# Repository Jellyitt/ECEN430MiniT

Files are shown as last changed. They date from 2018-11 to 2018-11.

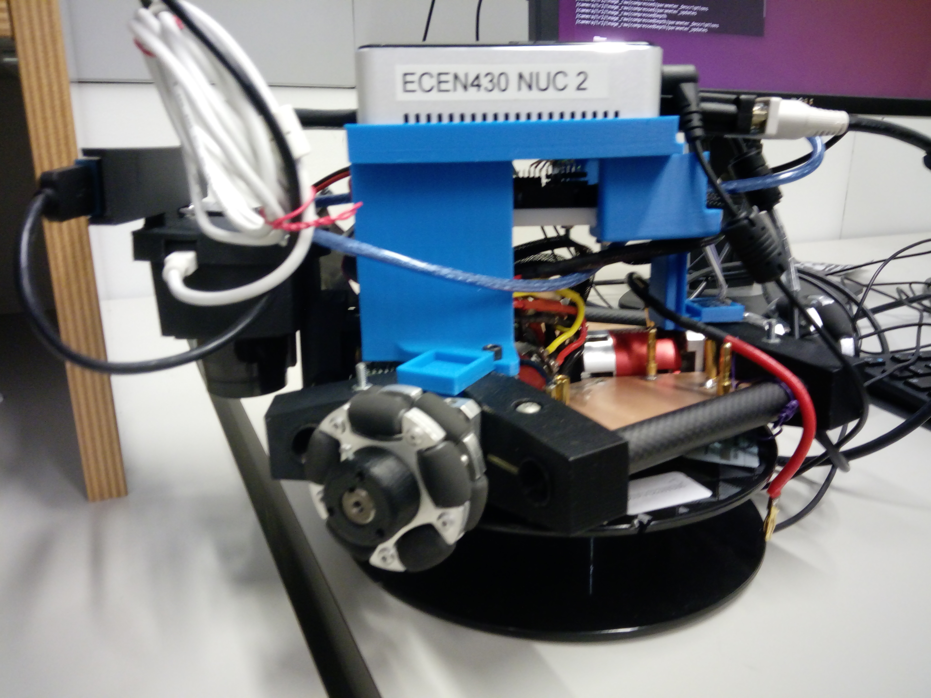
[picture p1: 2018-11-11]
Development Files/Hardware/IMG_20181106_105924.jpg

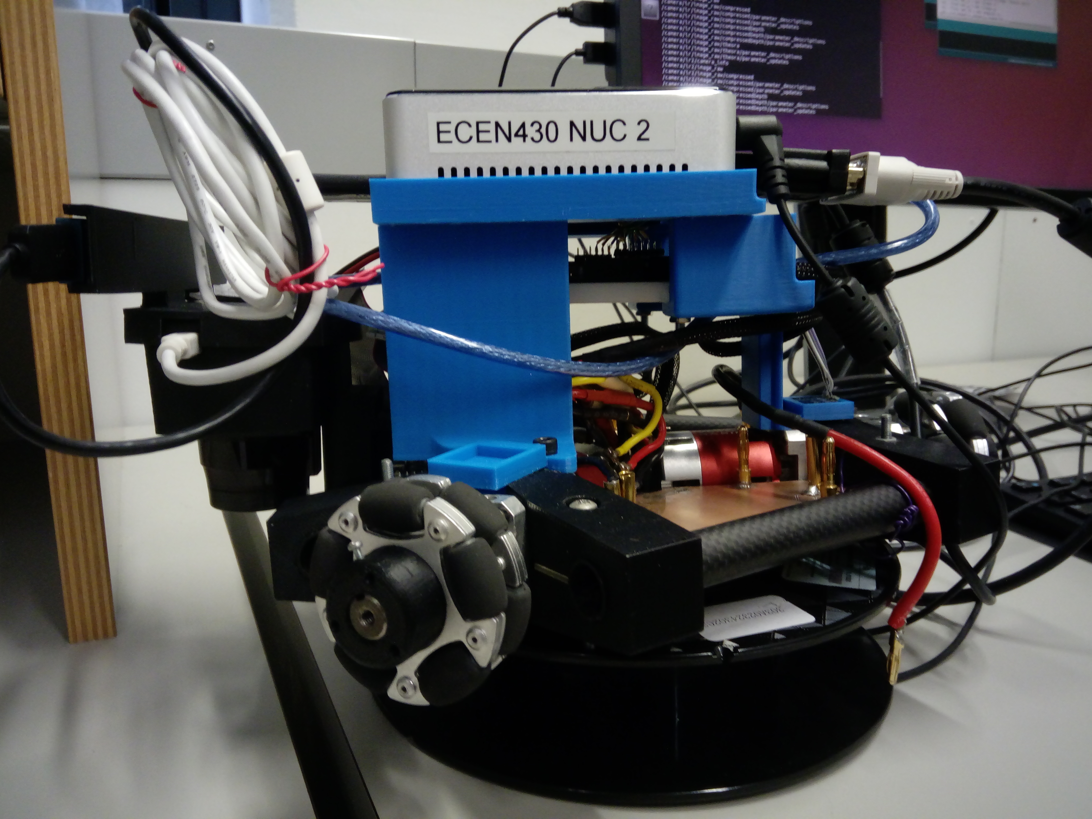
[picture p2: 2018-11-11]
Development Files/Hardware/IMG_20181106_105932.jpg

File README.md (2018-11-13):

# ECEN 430 Autonomous Vehicle Files

This was a collaborative project worked on during the course of ECEN 430 (2018)- Advanced Mechatronic Engineering 2: Intelligence and Design.

This autonomous vehicle imployed a ROS based system across a Intel NUC and a Laptop. Both computer systems were operating on Ubuntu 16.04.4. This was implemented on the Mini Triangle robot platform

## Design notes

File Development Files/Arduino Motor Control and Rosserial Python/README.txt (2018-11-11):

This system runs arduino 1.8.5
The code is a ROS node that communicates with the NUC through the rosserial_python node
This node subscribes to /cmd_vel and sends this for motor and speed control. While it publishes IMU data as geometry_msgs/Twist data type

How to run the arduino from terminal:
cd arduino-1.8.5/
./arduino

Note: Pressing tab on the keyboard autocompletes the word

File name:
Arduino Code - Motor Control - Bosch IMU -> Code using Bosch IMU
Arduino Code - Motor Control - MPU6050 IMU -> Code using MPU6050 IMU, used in the current system

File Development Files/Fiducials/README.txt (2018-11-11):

How to run fiducials in the current system set-up.
On the NUC currently:

Without launch files:
roscore
NT: roslaunch realsense_camera r200_nodelet_default.launch
NT: rosrun aruco_detect aruco_detect camera:=/camera/color/image_raw camera_info:=/camera/color/camera_info
NT: roslaunch fiducial_slam fiducial_slam.launch
NT: roslaunch fiducial_slam fiducial_rviz.launch

With launch files:
roscore
NT: cd catkin_ws/src/launch_file/launch
roslaunch min_launch2.launch

Note: NT = New Terminal

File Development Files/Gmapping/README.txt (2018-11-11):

How to run gmapping in the current system set-up.

Ensure both laptop and NUC are connected to the modesttriangle network.

Firstly turn on the NUC:
roscore
NT: cd catkin_ws/src/launch_file/launch
roslaunch min_launch.launch

On the laptop:
ssh modesttrianglenuc@modesttrianglenuc-desktop
NT: cd catkin_ws/src/slam_gmapping/gmapping/launch
roslaunch <File name>
NT: rviz

Note: NT = open new terminal window
Note: min_launch.launch = launches rosserial python node (arduino), Lidar, Camera and static transforms

<File name>:
gmap_move.launch -> runs gmapping, map server CO249, move base
gmap2.launch -> runs gmapping, map server CO level two floor plan
gmap249.launch -> runs gmapping, map server CO249
gmapping.launch -> runs gmapping node

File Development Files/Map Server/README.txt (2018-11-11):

How to run map_server in the current system set-up.

Ensure both laptop and NUC are connected to the modesttriangle network.

Firstly turn on the NUC:
roscore
{ NT: cd catkin_ws/src/launch_file/launch
roslaunch min_launch.launch }

On the laptop:
ssh modesttrianglenuc@modesttrianglenuc-desktop
NT: cd catkin_ws/src/launch_file/launch
roslaunch map_server.launch
NT: rviz

Note: NT = open new terminal window
      {} = optional

File name:
min_launch.launch = launches rosserial python node (arduino), Lidar, Camera and static transforms

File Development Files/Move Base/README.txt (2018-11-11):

How to run move_base in the current system set-up.

Ensure both laptop and NUC are connected to the modesttriangle network.

Firstly turn on the NUC:
roscore
NT: cd catkin_ws/src/launch_file/launch
roslaunch min_launch.launch

On the laptop:
ssh modesttrianglenuc@modesttrianglenuc-desktop
NT: cd catkin_ws/src/launch_file/launch
roslaunch <File name>
NT: rviz

Note: NT = open new terminal window
Note: min_launch.launch = launches rosserial python node (arduino), Lidar, Camera and static transforms

<File name>:
move_base.launch -> runs only move base node
move_base2.launch -> runs move base, map server, static transform
amcl_omni.launch -> runs move base, map server, static transform, amcl
all.launch -> runs move base, map server, static transform, amcl (old values in amcl)

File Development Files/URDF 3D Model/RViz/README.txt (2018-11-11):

How to run URDF model for RViz in the current system set-up.

Ensure both laptop and NUC are connected to the modesttriangle network.

Firstly turn on the NUC:
roscore
NT: cd catkin_ws/src/launch_file/launch
roslaunch min_launch.launch

On the laptop:
ssh modesttrianglenuc@modesttrianglenuc-desktop
NT: cd catkin_ws/src/simpleModel
rosrun simpleModel urdf_visualize.launch model:='$(find simpleModel)/urdf/simpleModel.urdf'

Note: NT = open new terminal window
Note: min_launch.launch = launches rosserial python node (arduino), Lidar, Camera and static transforms

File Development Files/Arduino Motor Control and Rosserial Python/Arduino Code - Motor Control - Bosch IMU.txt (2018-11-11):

//Bosch BNO055 libraries
#include <Wire.h>
#include <Adafruit_Sensor.h>
#include <Adafruit_BNO055.h>
#include <utility/imumaths.h>

//ROS libraries
#include <ros.h>
#include <ArduinoHardware.h>
#include <geometry_msgs/Twist.h>

//#define led_pin 13
#define max_x 1.5
#define max_y 1.5
#define max_Th 3

#define BNO055_SAMPLERATE_DELAY_MS (1000)

Adafruit_BNO055 bno = Adafruit_BNO055();

volatile float linear_v_x, linear_v_y, linear_v_z;
volatile float angular_v_x, angular_v_y, angular_v_z;

ros::NodeHandle nh;

//motor 1 -- Err(LOW) = forward motion/counter-clockwise
#define PWM1 6 //Port A, pin 31
#define En1 8 //Port A, pin 23
#define Err1 3 //Port A, pin 25

//motor 2 -- Err(HIGH) = forward motion/clockwise
#define PWM2 10 //Port A, pin 29
#define En2 7 //Port A, pin 19
#define Err2 5 //Port A, pin 21

//motor 3 -- Err(HIGH) = clockwise motion
#define PWM3 9 //Port A, pin 27
#define En3 4 //Port A, pin 15
#define Err3 2 //Port A, pin 17

void messageCb(const geometry_msgs::Twist& val){
  float val_x = val.linear.x;
  float val_y = val.linear.y;
  float val_Th = val.angular.z;
  int speed_x, speed_y, speed_Th;
  if(val_x == 0 && val_y == 0 && val_Th == 0){
    digitalWrite(En1, LOW);
    digitalWrite(En2, LOW);
    digitalWrite(En3, LOW);
  }
  else{
    int x = calcX(val_x);
    int y = calcY(val_y);
    int Th = calcTh(val_Th);

    if(x != 0 && Th != 0){
      if(Th > 0){
        speed_x = (-1*x)/4 + Th;
        speed_y = x/1.5 + Th;
        speed_Th = (-1*Th);
        }
        else{
        speed_x = (-1*x)/1.5 + Th;
        speed_y = x/4 + Th;
        speed_Th = (-1*Th);
        }
      }
    else{
      speed_x = (-1*x) + Th;
      speed_y = x + Th;
      speed_Th = (-1*Th);
    }
    
    set_dir(sign(speed_x, Th), sign(speed_y, Th), sign(0, speed_Th * -1));
    drive_motors(min(abs(0.7*speed_x), 229), min(abs(0.7*speed_y), 229), min(0.7*abs(speed_Th), 229));
  }
}

ros::Subscriber<geometry_msgs::Twist> sub("/cmd_vel", &messageCb );
geometry_msgs::Twist imu_msg;
ros::Publisher imu_data("imu/data", &imu_msg);

void setup() {
  TCCR1B = TCCR1B & B11111000 | B00000010; // for PWM frequency of 3921.16 Hz  -> pins 9 + 10
  TCCR2B = TCCR2B & B11111000 | B00000010; // for PWM frequency of 3921.16 Hz  -> pin 11

  pinMode(PWM3, OUTPUT);
  pinMode(En3, OUTPUT);
  pinMode(Err3, OUTPUT);
  pinMode(PWM2, OUTPUT);
  pinMode(En2, OUTPUT);
  pinMode(Err2, OUTPUT);
  pinMode(PWM1, OUTPUT);
  pinMode(En1, OUTPUT);
  pinMode(Err1, OUTPUT);
  //pinMode(led_pin, OUTPUT);
  
  linear_v_x = 0;
  linear_v_y = 0;
  linear_v_z = 0;
  angular_v_x = 0;
  angular_v_y = 0;
  angular_v_z = 0;
  
  bno.setExtCrystalUse(true);
 
  nh.initNode();
  nh.subscribe(sub);
  nh.advertise(imu_data);
}

void loop(){
  while(!nh.connected()){
  nh.spinOnce();
  imu_update();
  }
  
  //digitalWrite(led_pin, LOW);
  //delay(100);
  //digitalWrite(led_pin,LOW);
}

void imu_update(){
  imu::Vector<3> gyro = bno.getVector(Adafruit_BNO055::VECTOR_GYROSCOPE);
  linear_v_x = gyro.x();
  linear_v_y = gyro.y();
  linear_v_z = gyro.z();

  imu::Vector<3> accel = bno.getVector(Adafruit_BNO055::VECTOR_ACCELEROMETER);
  angular_v_x = accel.x();
  angular_v_y = accel.y();
  angular_v_z = accel.z();

  delay(BNO055_SAMPLERATE_DELAY_MS);

  // update geometry msg
  imu_msg.linear.x= linear_v_x;
  imu_msg.linear.y= linear_v_y;
  imu_msg.linear.z= linear_v_z;
  imu_msg.angular.x= angular_v_x;
  imu_msg.angular.y= angular_v_y;
  imu_msg.angular.z= angular_v_z;

  imu_data.publish(&imu_msg);

}

//Motor speeds
int calcX(float i){
  float speedFrac = i/max_x;
  return (int)(speedFrac*250);
}

int calcY(float i){
  float speedFrac = i/max_y;
  return (int)(speedFrac*250);
}

int calcTh(float i){
  float speedFrac = i/max_Th;
  return (int)(speedFrac*250);
}

//Motor Direction
int sign(float spd, float turn){
  if(turn != 0){
    if(turn < 0){
      return LOW;
    }
    else{
      return HIGH;
    }
  }
  else{
  if(spd < 0){
    return LOW;
  }
  else{
    return HIGH;
  }
  }
}

//Set motors
void set_dir(int sgn1, int sgn2, int sgn3){
  digitalWrite(Err1, sgn1);
  digitalWrite(Err2, sgn2);
  digitalWrite(Err3, sgn3);
}

void drive_motors(int pwm_1, int pwm_2, int pwm_3){
  digitalWrite(En1, HIGH);
  digitalWrite(En2, HIGH);
  digitalWrite(En3, HIGH);
  analogWrite(PWM1, pwm_1);
  analogWrite(PWM2, pwm_2);
  analogWrite(PWM3, pwm_3);
}

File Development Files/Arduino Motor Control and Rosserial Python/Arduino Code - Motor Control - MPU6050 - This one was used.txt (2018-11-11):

#include <MPU6050_tockn.h>
#include <elapsedMillis.h>
#include <ros.h>
#include <std_msgs/UInt16.h>
#include <geometry_msgs/Twist.h>

float max_x = 1.5;
float max_y = 1.5;
float max_Th = 5;

volatile float linear_v_x, linear_v_y, linear_v_z;
volatile float angular_v_x, angular_v_y, angular_v_z;

unsigned long publish_interval = 20; //ms

ros::NodeHandle nh;
MPU6050 mpu6050(Wire); //create mpu instance using wire lib

elapsedMillis timeElapsed;
elapsedMillis timePublish;

//motor 1 -- Err(LOW) = forward motion/counter-clockwise
#define PWM1 6 //Port A, pin 31
#define En1 8 //Port A, pin 23
#define Err1 3 //Port A, pin 25

//motor 2 -- Err(HIGH) = forward motion/clockwise
#define PWM2 10 //Port A, pin 29
#define En2 7 //Port A, pin 19
#define Err2 5 //Port A, pin 21

//motor 3 -- Err(HIGH) = clockwise motion
#define PWM3 9 //Port A, pin 27
#define En3 4 //Port A, pin 15
#define Err3 2 //Port A, pin 17

void messageCb(const geometry_msgs::Twist& val){
  float val_x = val.linear.x;
  float val_y = val.linear.y;
  float val_Th = val.angular.z;
//  int speed_x, speed_y, speed_Th;
  if(val_x == 0 && val_y == 0 && val_Th == 0){
    digitalWrite(En1, LOW);
    digitalWrite(En2, LOW);
    digitalWrite(En3, LOW);
  }
  else{
    int x = calcX(val_x);
    int y = calcY(val_y);
    int Th = calcTh(val_Th);
//    if(Th > 0){
//    speed_x = (-1*x)/2 - Th;
//    speed_y = x/2 - Th;
//    }
//    else{
    int speed_x = (-1*x) - Th;
    int speed_y = x - Th;
//}
    int speed_Th = (-1*Th);
    set_dir(sign(speed_x), sign(speed_y), sign(speed_Th));
    drive_motors(min(abs(0.9*speed_x), 229), min(abs(0.9*speed_y), 229), min(0.9*abs(speed_Th), 229));
  }
}

ros::Subscriber<geometry_msgs::Twist> sub("/cmd_vel", &messageCb );
geometry_msgs::Twist imu_msg;
ros::Publisher imu_data("imu_data", &imu_msg);

void setup() {
  TCCR1B = TCCR1B & B11111000 | B00000010; // for PWM frequency of 3921.16 Hz  -> pins 9 + 10
  TCCR2B = TCCR2B & B11111000 | B00000010; // for PWM frequency of 3921.16 Hz  -> pin 11
 
  pinMode(PWM3, OUTPUT);
  pinMode(En3, OUTPUT);
  pinMode(Err3, OUTPUT);
  pinMode(PWM2, OUTPUT);
  pinMode(En2, OUTPUT);
  pinMode(Err2, OUTPUT);
  pinMode(PWM1, OUTPUT);
  pinMode(En1, OUTPUT);
  pinMode(Err1, OUTPUT);

  mpu6050.begin();
  mpu6050.calcGyroOffsets(true);

  nh.initNode();
  nh.subscribe(sub);
  nh.advertise(imu_data);

}

void loop(){
  nh.spinOnce();
 
  if (timePublish >= publish_interval){
    imu_update();
    timePublish= 0;
  }

}

void imu_update(){
  mpu6050.update();

  // Update local variables 
  linear_v_x +=  mpu6050.getAccX()*(timeElapsed/1000.00);
  linear_v_y += mpu6050.getAccY()*(timeElapsed/1000.00);
  linear_v_z = mpu6050.getAccZ()*(timeElapsed/1000.00);
  angular_v_x = getGyroAngleX();
  angular_v_y = getGyroAngleX();
  angular_v_z = getGyroAngleX();
  timeElapsed = 0; //restart timer

  // update geometry msg
  imu_msg.linear.x= linear_v_x;
  imu_msg.linear.y= linear_v_y;
  imu_msg.linear.z= linear_v_z;
  imu_msg.angular.x= angular_v_x;
  imu_msg.angular.y= angular_v_y;
  imu_msg.angular.z= angular_v_z;

  imu_data.publish(&imu_msg);
  
}

int calcX(float i){
  float speedFrac = i/max_x;
  return (int)(speedFrac*250);
}

int calcY(float i){
  float speedFrac = i/max_y;
  return (int)(speedFrac*250);
}

int calcTh(float i){
  float speedFrac = i/max_Th;
  return (int)(speedFrac*250);
}

int sign(float i){
  if(i < 0){
    return LOW;
  }
  else{
    return HIGH;
  }
}

void set_dir(int sgn1, int sgn2, int sgn3){
  digitalWrite(Err1, sgn1);
  digitalWrite(Err2, sgn2);
  digitalWrite(Err3, sgn3);
}

void drive_motors(int pwm_1, int pwm_2, int pwm_3){
  digitalWrite(En1, HIGH);
  digitalWrite(En2, HIGH);
  digitalWrite(En3, HIGH);
  analogWrite(PWM1, pwm_1);
  analogWrite(PWM2, pwm_2);
  analogWrite(PWM3, pwm_3);
}

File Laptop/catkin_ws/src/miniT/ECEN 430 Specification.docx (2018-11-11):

Product Specification: Indeterminate Polygon

ECEN 430 Team 1 2018 T2

Name: Angus Tan ID: 300289679

The Mini Triangle robot platform is able to navigate with sensors inputs. It is capable of semiautonomous operation and fully autonomous movement between waypoints. The platform can detect and avoid obstacles while moving between waypoints. The platform is purposed to be able to map and localise itself within a warehouse environment. Mapping and localisation is done by utilising existing simultaneous localisation and mapping (SLAM) techniques. The platform will be adapted for driving forklifts in warehouses.

The omnidirectional robot can move in all directions without steering its wheels and can rotate clockwise and counter-clockwise with reference to their axis. This affords high mobility and makes the robot useful in a large variety of indoor environment.

The robot uses three Omni wheels that are each driven by a DC motor - Thunder Power Z3R. Each of the motors is connected to a gearbox with a 26:1 reduction gearing ratio; in turn controlled by three motor driver PCBs. Motor drivers are connected to the microcontroller to receive the movement commands. Two LiPo batteries are used to power the robot, each provides 7.4 V and 5000 mAh. The batteries have a series connection, doubling the nominal voltage to 14.8 V. Moreover, the boost converter input voltage is direct from the batteries and provides a constant 19 V supply to the NUC. This guarantees consistent power supply to the NUC as it mitigates voltage drop-off while the motors are running. The high current draw from the motors means that LiPo batteries are the ideal battery technology

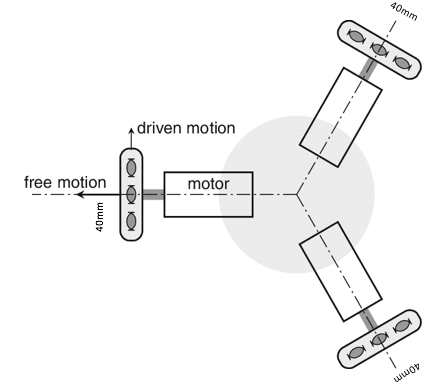
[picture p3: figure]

In order to perform SLAM, the platform is equipped with following sensors.

- Light Detection and Ranging (LiDAR) unit – Obstacle detection
- Inertial Measurement Unit (IMU) – Reports the acceleration and orientation of the platform
- 3D Depth Camera – Visualises the platform’s surrounding environment
- Odometry???

Locomotion & Power
3x DC Motor Thunder Power Z3R | - Status: discontinued - Type: Brushless - Size: 540 - # of Turns/Windings: 17.5 - Timing: Adjustable (0-50 degrees)
3x ESCON Motor Driver | http://storkdrives.com/wp-content/uploads/2013/10/MR_enUS_ESCON-Module-50-5.pdf
3x Gearbox BB BaneBots??? | - 26:1 Gearing ratio
3x Omni Wheel | - Diameter: 40 mm??? - Number of plates: 2 - Substrate: - Roller material: - Number of rollers: - Load capacity:
2x Turnigy Nano-tech 2S3P Hardcase Saddle LiPo pack | - 5000 mAh - 7.4 V - The nominal operating voltage for motor drivers is 10-15 VDC, hence two 2S in series (14.8 V) or a 3S (11.1 V) or 4S (14.8 V) LiPo is recommended.
YH11053A Boost Converter | - 7.4 V to 5 - 42 V - 4 A - A boost converter will step up the voltage to the 19 V required by the NUC

Operational Specifications
Recommended Users | The product is recommended for operators with experience in computers and basic electronics.
Input | Pre-mapped mapping data of the warehouse.
Power supply | Continuous operation is limited by battery capacity
Operation speed | Close to walking speed: 1 ms⁻¹
Area Coverage | - Square metres – limited by NUC RAM - The types of SLAM that are viable with this platform are limited by the refresh rate of the LiDAR – see localisation specifications
Assembly Environment | The components required to make this robot are manufactured by different companies. Hence an electronics lab or specialized workshop is recommended for assembling the robot.
Storage Environment | Because the majority of the robot is electronic components, the storage area should have low humidity. It should be stored at room temperature. This robot should not be stored in places which has high magnetic or electric fields.

Operational Environment

Well lit warehouse environment. Free of stairwells or low hanging potential obstacles.

- The robot should not be operated in environments where obstacles are present which are higher than the LiDAR or the height of the RealSense (??? mm)
- The environment should not have reflective objects as this may interfere with localisation
- The robot should be operated on solid, non-reflective floors
- The robot should not be operated on a sloped floor
- Autonomous operation should not be used is a room with stairwells
- The robot is able to traverses small obstacles, i.e. the saddle of a doorway
- The when removing batteries for charging, the sensors must not be unplugged. Doing so will cause the COM ports to reset and will require reconfiguring them.

Manufacture and Materials | The chassis of the robot is made of 3D printed ABS parts and carbo fibre tubing. The major components are the NUC, motors and driver units, LiDAR, camera and batteries. The components are sourced from multiple manufacturers to minimise the number of necessary items and cost of the robot. - The platform is made of high quality, easy to source components. - The platform is designed to be used around forklifts in a way that is safe for the operator and other workers.
Transportation | The sensors are delicate and very costly, hence while transporting the robot, precautions should be taken. The robot should not be tilted or jolted at any time, thus a cushioned or padded container should be used. An instruction manual is recommended to be included amongst the packaging.
Limitations | - The robot is not suitable for use in environments other than those recommended. - Service and maintenance should be conducted by knowledgeable persons or professionals. It is advised to contact the manufacturer service centre. - The robot must not be roughly or carelessly handled. - Continuous operation is limited by battery capacity. Multiple sets of batteries can extend operation time.
Safety Standards | During construction and operation of the robot, safety standards must be followed. Some International Standards Bodies are listed below: - IEC - ISO - ANSI

Dimensions | Width: 280 mm Length: 320 mm Ground clearance: 7mm Weight 2.5 ± 0.05 kg Turning radius: ??? mm Wheelbase width: ??? mm Wheelbase length: ??? mm

Sensors & SLAM
Intel NUC6i5SYK | - Status: discontinued - Processor: Dual-core Intel Core i75557U CPU with multi-threading - Speed: 3.10GHz - RAM: 16 GB - Compact size: 112 mcm x 116 mm x 36 mm - Input voltage: 12- 19V - Low power consumption: 28 W
Arduino Uno Rev 3 | - Input voltage: 7 – 12 V (pins) or 5 V (USB connector) - The voltage can be stepped down for the Arduino Uno
MPU 6050 IMU | - Input Voltage: 2.3 – 3.4 V - Gyroscope sensitivity: 131 LSBs/dps
Intel RealSense R200 | - Status: discontinued - 5 V 900 mA - 0.5 m - 3.5 m Indoor operating range - 640x480 Range depth resolution and IR at 60 FPS - 1080p RGB at 30FPS - Connection: USB 3.0 port
Hokuyo URG-04LX-UG01 LiDAR | - 10 Hz 5 V - 0.36° Resolution - 240° Range - 20 – 5600 mm Range
Odometry???
TP-Link TL-802N Wireless Router | - Powered via micro USB Port - External Power Supply: 5 V at 1 A - 300 Mbps data rate - Operating temperature: 0°C-40°C - Operating humidity: 10%-90% non-condensing
Cables | - 1x USB A – micro USB - 1x USB A –mini USB - 1x USB A to B - 1x USB 3.0 A to Micro-B Male

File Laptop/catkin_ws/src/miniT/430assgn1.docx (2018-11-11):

Mechatronic Design and Evaluation

ECEN430 Team 1 2018 T2

Name: Angus Tan ID: 300289679

Introduction

Key functionalities of robots tasked with localisation techniques include autonomous exploration of unknown sites and recognition of objects of interest. Open source software modules are often used for the development of such complex capabilities which include simultaneous Localization and Mapping (SLAM) for self-localization and mapping in an urban environment.

Increased autonomy level is an area of research that has the potential to vastly improve the operation of autonomous robots. The use of freely available reusable and adaptable open source software can significantly reduce development time and increase robot capabilities. Robot Operating System (ROS) [1] is used as the robot middleware for the software modules. It has been widely adopted in robotics research and can be considered a de-facto standard.

Hardware dependent modules like cameras and motor drivers are assumed to provide the necessary sensor data according to existing ROS standards and are steerable by velocity commands.

The criteria selection and evaluation results of the six NIARC robots are presented in the following sections. The components currently presented on the platforms were considered, as well as the missing components which are required for full operation.

Location and Mapping

Creating maps of the environment is important for two reasons: performing situation assessment and localizing the platform inside buildings and for path planning and high level autonomous behaviours. While purely geometric maps such as occupancy grid maps are useful for navigation and obstacle avoidance, additional semantic information like the location of objects of interest is required for intelligent high level autonomous behaviour control [4]. SLAM Robots have to be considered as operating in unknown environments as to be most robust against changes in order to generate sufficiently accurate metric maps useful for navigation of a robot system. As odometers are notoriously unreliable, hector slam is designed to not require odometry data, instead purely relying on fast LIDAR data scan-matching at full LIDAR update rate [3]. As hector slam is dependent upon the sampling rate of the LiDAR, while these are more resource intensive implementing, gmapping or rgbdslam can be practical. Combined with an attitude estimation system and an optional pitch/roll unit to stabilize the laser scanner, the system can provide environment maps even if the ground is non-flat

The full six degrees of freedom can be realized in the implementation of an Extended Kalman Filter (EKF) and fuses measurements from an inertial measurement unit (IMU), the 2D mapping from the LiDAR and optionally from additional localization sensors like cameras [2]. The filter is primarily driven by the IMU, without using the control inputs or wheel odometry as they typically are unreliable due to wheelspin or side drift on the ground.

Platform Analysis

In order to fully realise the goal of localisation and mapping within a given indoor environment, for example, a warehouse, the manoeuvrability of the platform and how freely it is able to turn is vital. This is closely related to slippage of the platform while it traverses its environment. For this reason, the six platforms considered all used wheels rather than continuous tracks. Wheels present distinct advantages in reduced slipping, higher manoeuvrability, and lower production costs when compared to tracks [5].

While a tracked platform may be able to traverse larger obstacles with increased power efficiency due to higher traction, these were not deemed to outweigh their disadvantages such as encoder errors, given the types of environments the platform will be deployed in. Similarly, as the platform is to be deployed on a solid, mostly flat surface such as a warehouse floor, the weight and height of the platform are not vital but weight should be minimised to increase power efficiency.

As previously stated, the ability to travel over small obstacles, for example, the saddle in a doorway, is important when considering functionality the platform is tasked with. Thus, it is important to consider the ground clearance of each of the six platforms.

Soft constraints were also looked into, ideally, a platform should have minimal work done in order for it to be viable, reducing further costs and time spent. Also, development software should be familiar or readily available, further reducing time costs. The following paragraphs detail the analysis of the viability of each of the platforms given their specifications when weighed against the recommended criteria.

Bolt

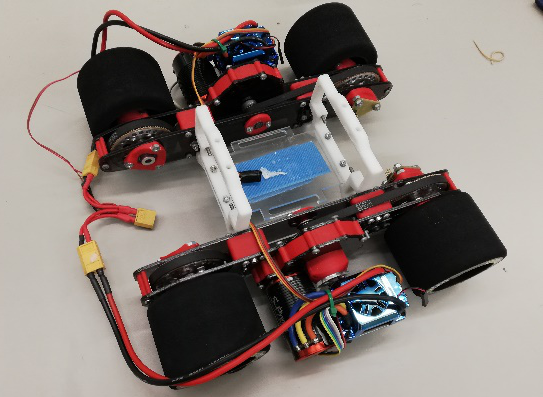
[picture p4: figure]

This platform is almost complete, missing a LiDAR, IMU, and development board. An ams AS5048A 14-bit rotary sensor is present on each motor, which affords a resolution of 16384 positions per full revolution of the motor. The platform’s ability to rotate and perform precise manoeuvres is however poor, in addition to its low clearance. This is due to the choice of motor and motor drivers, which are the Toro S-Pro4 and Toro TS150, respectively; which are designed for high-speed RC applications. Moreover, a track is present on each side of the platform to drive both of the wheels on one side at the same speed, essentially this is a tracked platform. 30:1 gear reduction is present on Bolt to reduce its speed, linked to each of the motors.

Power requirements of Bolt are as follows: the motor drivers require a 2S to 6S LiPo battery pack where each LiPo cell has a nominal voltage of 3.7 V connected in series; this is equivalent to a total of 7.4 – 22.2 V.

This platform does not meet the criteria for the specification, hence it is not suitable.

Dimension | Parts included | Missing Parts
W:32cm L:28.5 Clearance: 7mm | 2x Motor Drivers 2x 3 Phase Motors 4x 80mm Racing Tires 2x 14-bit Magnetic rotary sensor | Microcontroller IMU Lidar mount

Triangle

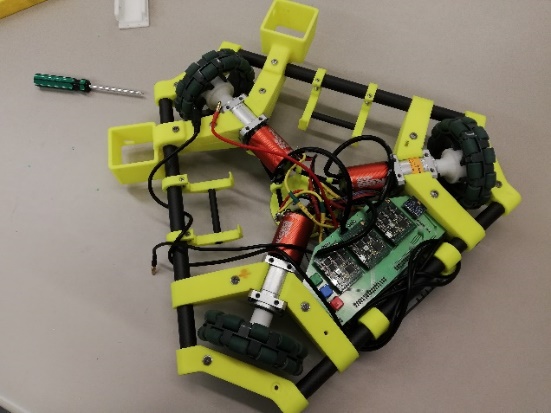
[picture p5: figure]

The triangular three-wheeled design presents advantages in decreased risk of wheel slippage and is able to better manoeuvre in a closed environment.

The use of Omni wheels presents great manoeuvrability and control in movement, driven using Tekin ROC 412 DC motors, gearboxes with a 2:1 gearing ratio is used to reduce the speed from the motors. Maxon 438725 servo controllers allow highly efficient control of the motors. Except for LiDAR, all required sensors are present. A power supply is also required. Two LiDAR mounts are present, as presumed if using one LiDAR, one mount should be shifted on the front of the platform in order to optimise the field view. The platform is fitted with a myRIO evaluation board, LabVIEW is required if using the board. To reduce time cost, it is recommended to use an Arduino to interface with ROS, which is likely to be a more familiar interface.

The operating voltage for the ROC412 motor drivers is 10-15VDC, hence a 12 V battery is suitable for this platform. Voltage regulation must also be performed in order to power the microcontroller, typically 9 V for an Arduino Uno.

This platform is ranked third, its meets all the necessary criteria but requires modifications to the existing structure.

Dimension | Parts included | Missing Parts
W: 44cm L: 39cm Clearance:12mm | 3x DC motors 3x Motor Drivers 3x Gearboxes BB 26:1 1x IMU 1x Mouse sensor 3x 100mm Omni wheels 2x Lidar Mounts | Battery Microcontroller LiDAR

Mini-Triangle

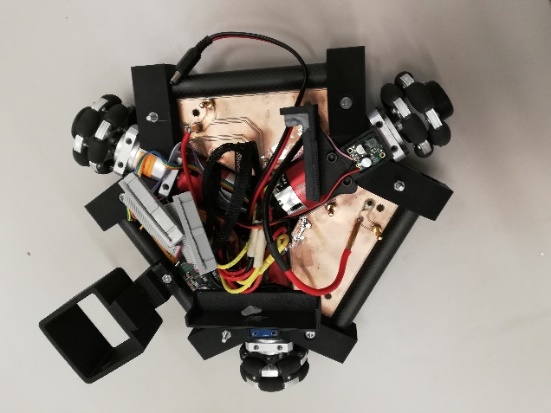
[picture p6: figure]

As its name suggests, this platform is similar to the previously discussed triangle, differing in its smaller size. Again, it requires a LiDAR unit and a power supply, as well as a development board. A single LiDAR mount is present on the front end of the platform. It was found that a power connector to one of the DC motors was broken, needing to be soldered into place, this is a trivial fix and does not negatively impact the viability of the platform. A ribbon-to-USB adapter is required to interface the motor driver breakout board to the microcontroller.

The nominal operating voltage for motor drivers is 10-15 VDC and can be stepped down for the microcontroller, hence a 3S, 4S LiPo or 12V battery is recommended.

Mini-Triangle is ranked first among the platforms considered as its design is optimal and sensors are already optimised, needing minimal repairs.

Dimension | Parts included | Missing Parts
W: 28cm L:32cm Clearance: 7mm | 3x DC motors Thunder Power Z3R 3x motor drivers 3x gearboxes BB 26:1 1x IMU 1x Mouse sensor 3x 40mm Omni Wheels 1x Lidar mount | Broken power connector Battery Microcontroller Ribbon-USB adapter

PWNBot

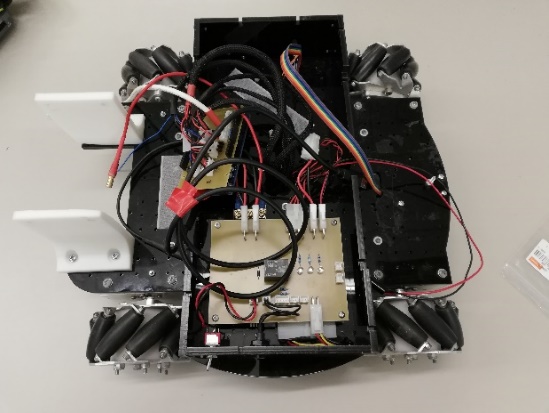
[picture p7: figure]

PWNBot is another Mecanum wheel based platform, missing components are encoders, LiDAR, and IMU. As it has 100 mm Mecanum wheels, the platform is afforded three degrees of freedom but is prone to slippage, which will result in erroneous tracking in its movements. An Arduino Mega affords interfacing with ROS. An ADNS-9800 laser motion sensor is presented on the underside of the platform to track its movement. Power requirements are as follows: the Maxon 230572 Motor Drivers require a nominal operating voltage of 10–50 V. The Hall sensor present on the platform requires 12 V DC. A M4-ATX DC power supply is present on the board which requires a 6-30 V input; hence a 2S LiPo or equivalent voltage battery is sufficient.

This platform is ranked second, its meets the recommended criteria but has some design flaws.

Dimension | Parts included | Missing Parts
W:37cm L:29.5cm H: 16cm Clearance:1cm | 4x Maxon Geared motors 4x Maxon motor drivers 4x 100mm Mecanum Wheels Arduino Mega Mouse sensor DC-DC power supply | Battery LiDAR IMU LiDAR mount

Michelangelo:

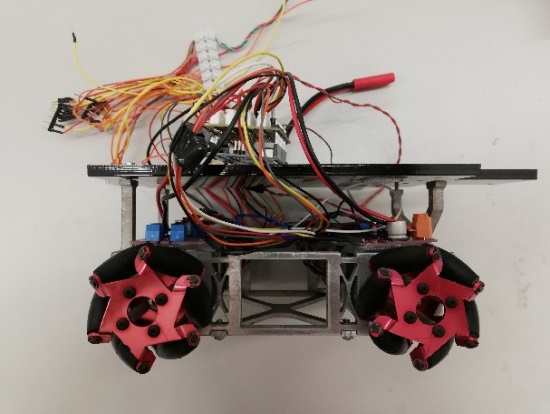
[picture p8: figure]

Michelangelo is a Mecanum wheel-based platform; most of the components are present except for the exteroceptive sensors, power supply and battery. This platform is driven by four NEMA 17 ST42STH47 stepper motors with STMicro L6470 motor driver units. The 40 mm Mecanum wheels afford the platform three degrees of freedom, however, it has weaknesses which are: difficult to calculate kinematics and inaccurate movement should slippage occur, this can be overcome with sensor fusion or EKF. An Arduino Uno is present which can be interfaced with ROS, along with a fused breakout board interfacing the Arduino with the motor drivers. Regarding sensors, an IMU, LiDAR, LiDAR mount and some type of odometry sensor are needed. Based off these assessments, this will add to parts cost as well as time spent waiting for parts to arrive. Based on the requirements of the motor drivers, a 5 V battery or 2S LiPo is sufficient to power the platform.

With necessary repairs and design changes, this platform can be suited to the task and it ranked fourth among the six platforms.

Dimension | Parts included | Missing Parts
W: 19CM L: 25cm Clearance: 6mm | 4x Stepper motors 4x Motor Drivers 4x 40mm Mecanum Wheels Arduino Uno Fused Breakout Board Lidar Mount | Encoder LiDAR IMU Battery

Bean MK1

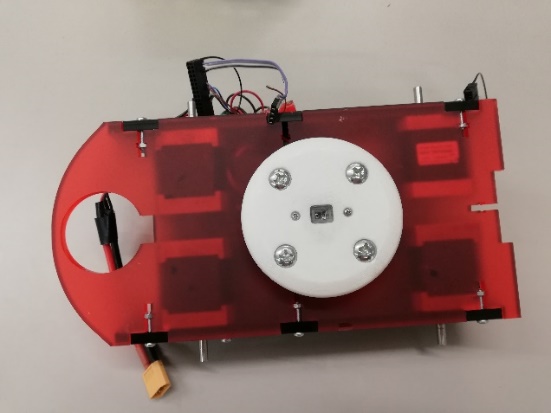
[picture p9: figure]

This platform is driven by four NEMA 17 ST42STH47 stepper motors with STMicro L6470 motor driver units, however encoders and wheels are not present. A mouse sensor is present which allows for tracking the movement of the platform. A LiDAR mount is present, designing an additional mount for the IMU is trivial in terms of overhead. In order for the platform to function, it will require: four wheels, an encoder for each wheel, a LiDAR, an IMU, and a development board. The mouse sensor on the underside of the platform has a range of 1 to 5 mm, as it cannot be moved upwards to clear obstacles, the clearance is limited to under 5mm. Furthermore, a battery will need to be procured; based on the requirements of the motor drivers, a 5 V battery or 2S LiPo is sufficient to power the platform. Based off these assessments, this will add to parts cost as well as time spent waiting for parts to arrive.

This platform does not fully meet the criteria for the task and is not suitable for the specification.

Dimension | Parts included | Missing Parts
L: 25cm W: 16CM | 4x Stepper motors 4x Motor Drivers Mouse Sensor Lidar Mount | 4x wheels LiDAR Microcontroller IMU Battery

Conclusion

An in-depth analysis was performed on the six robotic platforms, showing the advantages and disadvantages presented by each of the platforms. Based on how the platforms meet the set criteria, as ranking was found showing the viability of these platforms for the prescribed task; as follows: Mini-Triangle, PWNBot, Triangle, Michelangelo, and Bean MK1. The design of the platform was found to be crucial to the feasibility of each of the platforms, in particular the locomotive system and choice of wheels.

The choice of SLAM solution was found to be dependent on the environment for the specification, as well as the capabilities of the LiDAR system.

Bibliography

[1] Quigley, M., Gerkey, B., Conley, K., Faust, J., Foote, T., Leibs, J., Berger, E., Wheeler, R., Ng, A: ROS: an open-source Robot Operating System. In: ICRA workshop on open source software. Volume 3. (2009)

[2] Embedded Systems Architecture for SLAM Applications https://arxiv.org/ftp/arxiv/papers/1702/1702.01295.pdf

# [3] Teaching Robots Presence: What You Need to Know About SLAM

https://blog.cometlabs.io/teaching-robots-presence-what-you-need-to-know-about-slam-9bf0ca037553

[4] Hector Open Source Modules for Autonomous Mapping and Navigation with Rescue Robots http://citeseerx.ist.psu.edu/viewdoc/download?doi=10.1.1.435.9600&rep=rep1&type=pdf

[5] Wheels vs Continuous Tracks: Advantages and Disadvantages https://www.intorobotics.com/wheels-vs-continuous-tracks-advantages-disadvantages/

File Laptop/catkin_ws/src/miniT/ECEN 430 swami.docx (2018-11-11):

Product Specifications

Δ

Modest Triangle

The robot which has the ability to navigate with limited sensor is Modest Triangle. This robot has the ability to map and localize in a warehouse environment by utilizing existing SLAM techniques. This robot is being designed specifically for driving forklifts in warehouse. This robot can detect and avoid obstacles. It moves by using multiple local points.

Intel NUC | The NUC is a mini desktop PC, used for mobile robots which has single-board computing system - Processor: Dual-core Intel Core i75557U CPU with multi-threading - Speed: 3.10GHz - RAM: 16 GB - Power requirement: low (28 W) - Size: small (10 x 10 cm)
Sensors | - LIDAR - Real-Sense - QR code Scanner
Essentials | - Product CollectionIntel® RealSense™ Cameras (https://ark.intel.com/products/series/85364/Intel-RealSense-Cameras) - Code NameProducts formerly Double Springs (https://ark.intel.com/products/codename/81563/Double-Springs) - StatusDiscontinued - Launch DateQ3'15 - Depth TechnologyActive Stereo
Operational Specifications | - Operating Range (Min-Max)0.5m - 3.5m - Depth Resolution and FPS480 x 360 @ 60fps - Depth Field of ViewH: 59, V: 46, D: 70
Input | - Pre mapped data of the warehouse - Giving the robot global start and goal points - Sending the robot local destination points when required
Power Supply | Watt-hr
Area coverage | Square-meter
Performance | - The operation speed of the robot is same as walking speed - It can be used continuously with appropriate continuous power supply
Environment | - Manufacture: The components required to make this robot is being manufactured by different companies separately. Hence an electronic lab or specialized workshop will be the best place for assembling the robot - Storage: Because this robot is majorly made of electronic components, the storage area should definitely have very low humidity. It should be stored at room temperature. This robot should not be stored in places which has high magnetic or electric fields - Use: This robot is designed for warehouse environment.
Mapping | - Maplab: It is an research oriented visual inertial mapping framework. It is written in C++ language. It is ready to use. Since we require a map of the area, we need to map the area multiple times so that the results can be compared and maximum of errors can be eliminated. Maplab allows multi session mapping and also loop closure. - RTAB - RViz

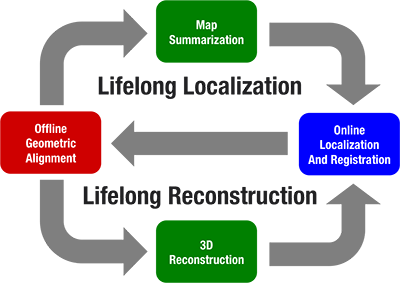
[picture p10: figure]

Localization | ROVIOLI: research oriented visual inertial mapping and localization framework. This ROVIOLI using maplab has great features: - Robust visual-inertial odometry with localization - Large-scale multisession mapping and optimization - Dense reconstruction - A research platform extensively tested on real robots
Citation for ROVIOLI and Maplab | @article{schneider2018maplab, title={maplab: An Open Framework for Research in Visual-inertial Mapping and Localization}, author={T. Schneider and M. T. Dymczyk and M. Fehr and K. Egger and S. Lynen and I. Gilitschenski and R. Siegwart}, journal={IEEE Robotics and Automation Letters}, year={2018}, doi={10.1109/LRA.2018.2800113} }
- Dependencies of Robust visual-inertial odometry with localization | - ros - kindr (https://github.com/ethz-asl/kindr) - lightweight_filtering (as submodule, use "git submodule update --init --recursive") #!command catkin build rovio --cmake-args -DCMAKE_BUILD_TYPE=Release
Install maplab with opengl scene | - Installation on Ubuntu 14.04 or 16.04 (https://github.com/ethz-asl/maplab/wiki/Installation-Ubuntu) - Introduction to the maplab framework (https://github.com/ethz-asl/maplab/wiki/Introduction-to-the-Maplab-Framework) - Structure of the framework (https://github.com/ethz-asl/maplab/wiki/Structure-of-the-framework) - Running ROVIOLI in VIO mode (https://github.com/ethz-asl/maplab/wiki/Running-ROVIOLI-in-VIO-mode) - Basic console usage (https://github.com/ethz-asl/maplab/wiki/Basic-Console-Usage) - Console map management (https://github.com/ethz-asl/maplab/wiki/Console-map-management)
Citation for Localization | @inproceedings{lynen2015get, title={Get Out of My Lab: Large-scale, Real-Time Visual-Inertial Localization.}, author={Lynen, Simon and Sattler, Torsten and Bosse, Michael and Hesch, Joel A and Pollefeys, Marc and Siegwart, Roland}, booktitle={Robotics: Science and Systems}, year={2015} }
Additional citation for ROVIOLI and maplab | @article{bloesch2017iterated, title={Iterated extended Kalman filter based visual-inertial odometry using direct photometric feedback}, author={Bloesch, Michael and Burri, Michael and Omari, Sammy and Hutter, Marco and Siegwart, Roland}, journal={The International Journal of Robotics Research}, volume={36}, number={10}, pages={1053--1072}, year={2017}, publisher={SAGE Publications Sage UK: London, England} }
Quantity and Manufacture | The robot has to be made as individual items as they have many important components and the number of requirement of this robot is less.
Materials | The materials required for making the robot depends on the environment it is exposed to. The frame of the robot is made with good quality plastic material. The major materials in this robot are NUC, motor, LIDAR, Real-Sense, motor driver, battery. LIDAR and Real-Sense are the two major sensors. NUC is the processor of the robot.
Quality | The quality of the robot is good. It contains quality products for its sensors and processor.
Standards | While designing and operating robots safety standards has to be followed such as: - American National Standards Institute (ANSI) U.S. Standards Body including CSA, BSI, DIN, AFNOR, JISC and more - International Organization for Standardization (ISO) International Standards Body - International Electrotechnical Commission (IEC) International Standards Body
Packaging and shipping | The components of this robot are very delicate and are costly. So while packing this robot precautions are to be taken so that the robot does not get damaged while shipping. The robot should not be tilted and perfect cushion should be provided as well. And instruction manual should be in the packing as well. High quality shipping should be made as the item is costlier and unique.
Aesthetic | The product is easy to use with user manual and some computer knowledge.
Ability of the product | - High Quality: The product is made with high priority of quality - Safety: As the product is used in forklift workshops the product is designed in such a way that it is safer for operator and workers. - Reliability: With less percentage of error the reliability is high.
Limitations | - This robot has to be properly handled - Rough handling is not advisable - Service and maintenance has to be carried out only by professionals and it is advisable to contact the company service centre - This robot is not suitable for other types of environment as it is being designed specifically - This robot cannot be used continuously for longer period

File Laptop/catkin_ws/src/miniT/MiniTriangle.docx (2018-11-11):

MiniTriangle:

The robot uses 3 Omni wheels (Width: 40mm) that are driven by 3 DC motors -Thunder Power Z3R -. Omnidirectional robot can move in all directions without steering their wheels and it can rotate clockwise and counter-clockwise with reference to their axis. This makes the robot useful in a large variety of indoor environment. It provides high mobility in comparison to the more common car-like robots. The motors are connected to gearboxes of 26:1 ratio along with three motor driver PCBs. Motor drivers are connected to the microcontroller to receive the movement command from it. 2 Li-Po batteries are used to run the robot and each could provide a 7.4V and 5000mAH. Moreover, boost converter gets its input voltage from the batteries and the output goes to the NUC as the NUC needs a 19V input.

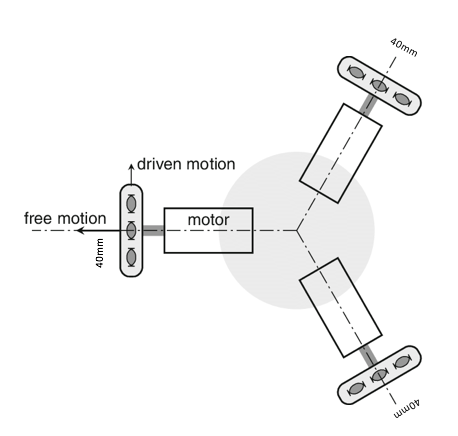
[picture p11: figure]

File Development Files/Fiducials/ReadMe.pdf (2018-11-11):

## Fiducial SLAM Configuration

To install the fiducial software from binary packages:

sudo apt-get install ros-kinetic-fiducials

Fiducial markers can be generated with a command like this:

rosrun aruco_detect create_markers.py 100 112 fiducials.pdf

Two nodes should be run, aruco_detect, (http://wiki.ros.org/aruco_detect) which handles the detection of the fiducials,
and fiducial_slam, (http://wiki.ros.org/fiducial_slam) which combines the fiducial pose estimates and builds the map and makes an estimate of the robot's position. The map is in the form of a text file (map.txt) specifying the 6DOF pose of each of the markers, and is automatically saved.

To launch the two nodes use the following command:

roslaunch aruco_detect aruco_detect.launch

roslaunch fiducial_slam fiducial_slam.launch

Remapping:

The camera and aruco_detect might not be linked together. This raises the issue of not being able to detect the markers despite fiducial_slam and aruco_detect are running. Thus remapping inside the aruco_detect launch file was necessary in order to make it works. The following command does the remapping from the terminal as the aruco_detect can accept arguments.

rosrun aruco_detect aruco_detect camera:=camera/color/image_raw camera_info:= /camera/color/camera_info

A launch file is also provided to visualize the map in rviz. (http://wiki.ros.org/rviz)

roslaunch fiducial_slam fiducial_rviz.launch

Generated Map

The map file is a text file with a line for each fiducial id: `

id x y z pan tilt roll variance numObservations links

x, y and z specify the translation of the fiducial from the origin in meters, and pan, tilt,
and roll specify its orientation in degrees. The fields variance and numObservations represent how good the pose estimate is considered to be, and how many observations were used to generate it. links is a list of the ids of fiducials that have been observed at the same time as the current fiducial. The coordinate frame used is the map frame, which is relative to the floor, so markers of the ceiling will have been rotated. The supplied launch files specify the map file
as ~/.ros/slam/map.txt.

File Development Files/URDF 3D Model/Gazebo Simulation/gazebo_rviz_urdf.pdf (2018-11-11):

# Running Gazebo

Install gazebo:

sudo apt-get install ros-%kinetic%-simulator-gazebo

Setup:

source ~/catkin_ws/devel/setup.bash

This launches gazebo:

roslaunch gazebo_ros empty_world.launch

Spawn urdf with the following where “object.urdf” is the name of your urdf and “1” is the height at which the model is spawned (m).

rosrun gazebo spawn_model -file `pwd`/object.urdf -urdf -z 1 -model my_object

# urdf in RViz

This assumes that you have an existing urdf file complete with launch packages etc, else see here to create a model from scratch: http://wiki.ros.org/urdf/Tutorials/Building%20a%20Visual%20Robot%20Model%20with%20UR DF%20from%20Scratch (http://wiki.ros.org/urdf/Tutorials/Building%20a%20Visual%20Robot%20Model%20with%20URDF%20from%20Scratch)

Or here for a SolidWorks exporter: http://wiki.ros.org/sw_urdf_exporter

To open the file in RViz, enter the following where “simpleModel” is the package name and “simpleModel.urdf’ is the name of the file:

roslaunch simpleModel urdf.visualize.launch model:=’$(find simpleModel)/urdf/ simpleModel.urdf’

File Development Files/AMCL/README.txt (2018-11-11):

How to run AMCL in the current system set-up.

Ensure both laptop and NUC are connected to the modesttriangle network.

Firstly turn on the NUC:
roscore
NT: cd catkin_ws/src/launch_file/launch
roslaunch min_launch.launch

On the laptop:
ssh modesttrianglenuc@modesttrianglenuc-desktop
NT: cd catkin_ws/src/launch_file/launch
roslaunch amcl_omni2.launch

Note: NT = open new terminal window

File name:
amcl_omni2.launch -> runs map_server and AMCL nodes
amcl_omni.launch -> runs map_server, AMCL, move base and a static transform

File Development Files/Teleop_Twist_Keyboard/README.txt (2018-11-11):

How to run teleop_twist_keyboard in the current system set-up.

Ensure both laptop and NUC are connected to the modesttriangle network.

Firstly turn on the NUC:
roscore
NT: cd catkin_ws/src/launch_file/launch
roslaunch min_launch.launch

On the laptop:
ssh modesttrianglenuc@modesttrianglenuc-desktop
NT: rosrun teleop_twist_keyboard teleop_twist_keyboard.py
NT: rviz

Note: NT = open new terminal window

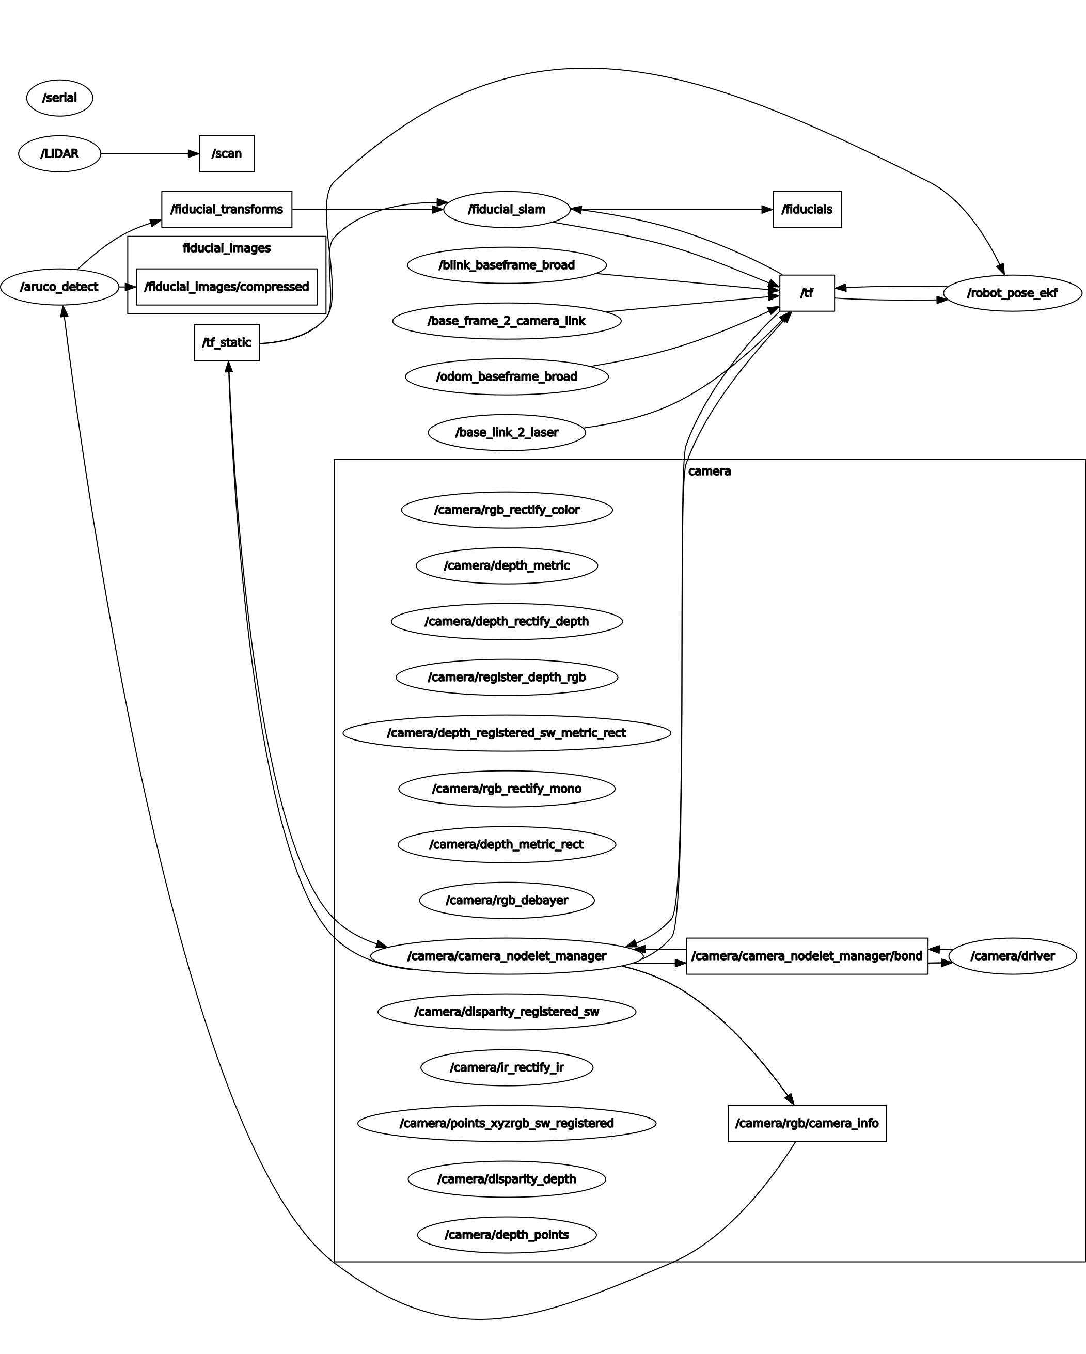
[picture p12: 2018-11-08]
NUC/catkin_ws/rosgraph.png

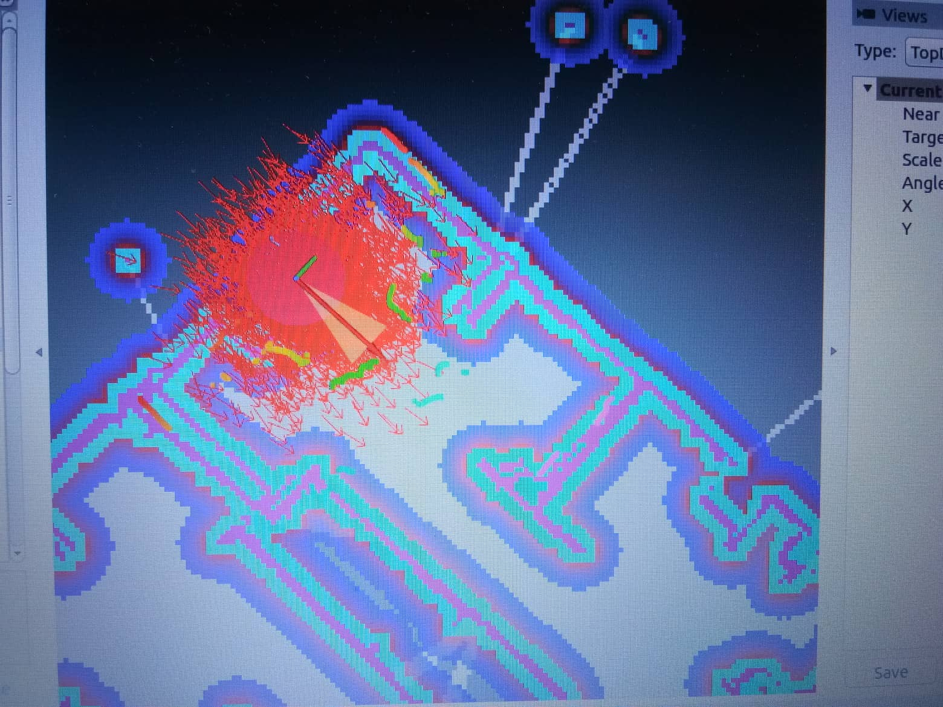
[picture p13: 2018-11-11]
Development Files/Integrated AMCL, MOVE BASE, MAP SERVER/45610283_741901529536008_8422294596733632512_n.jpg

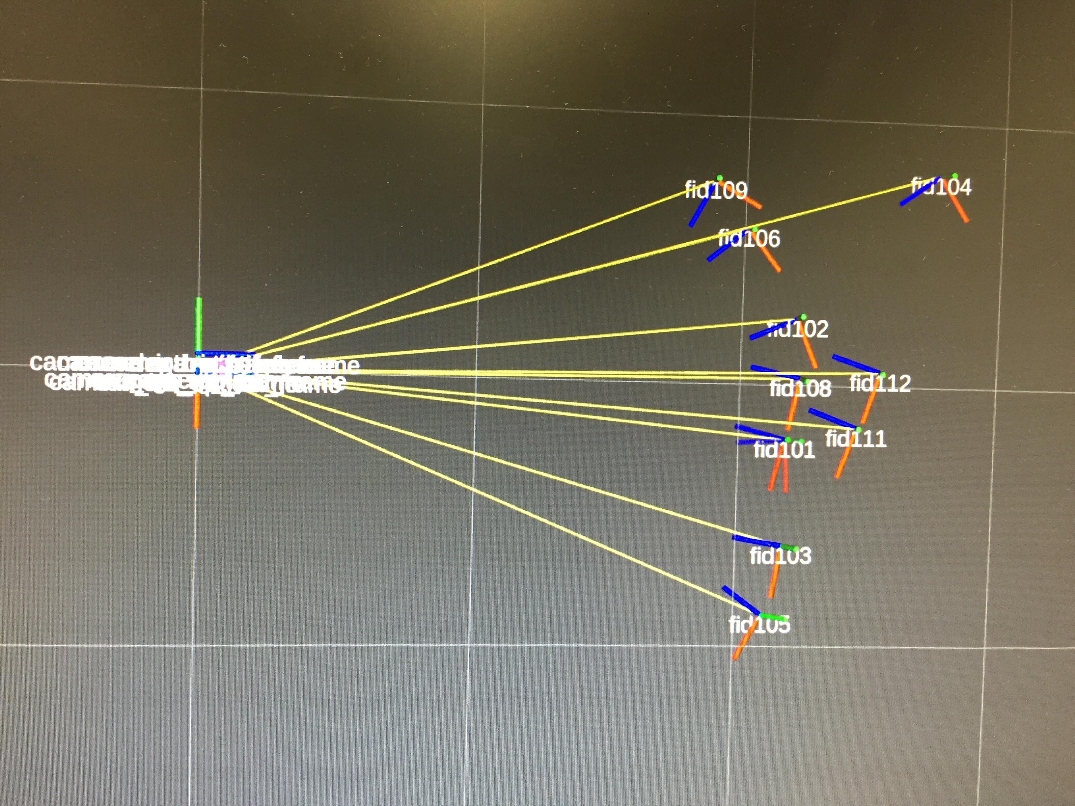
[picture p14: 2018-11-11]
Development Files/Fiducials/Images + Videos/45497587_2270631393168945_2697462843137064960_n.jpg

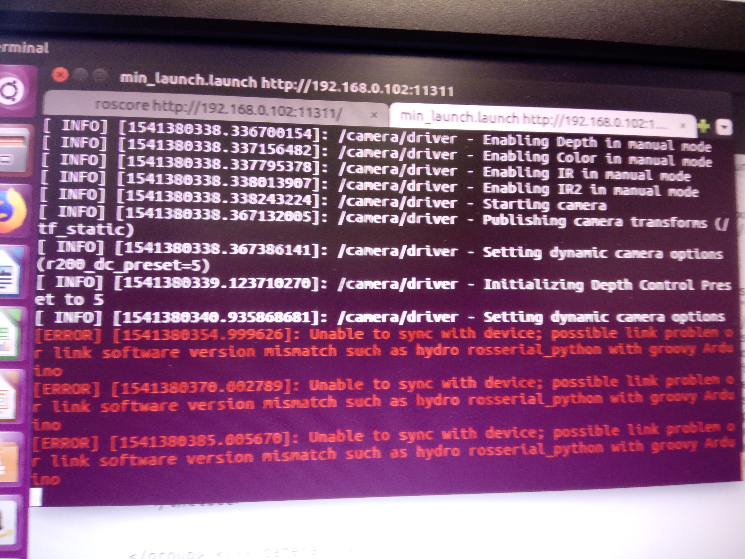
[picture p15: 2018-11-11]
Development Files/Arduino Motor Control and Rosserial Python/unsuccessful rosserial and but successful launching all other sensor nodes.jpg

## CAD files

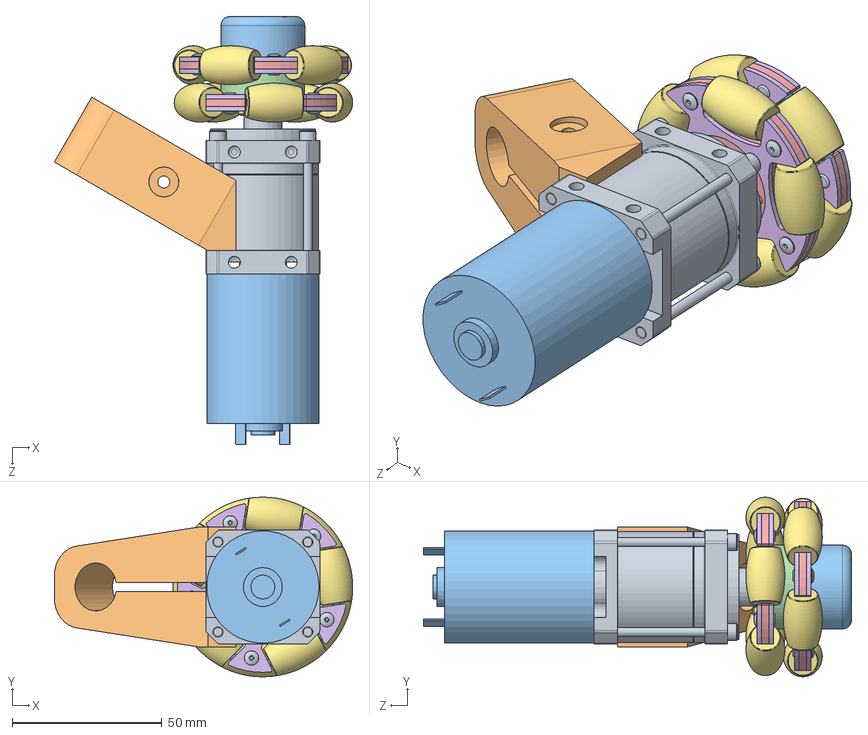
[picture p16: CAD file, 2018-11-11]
Development Files/Mini Triangle Solidworks - PCB Files/SolidWorks Model/Corner Assembly.SLDASM
99.6 x 60.0 x 142.9 mm
Gearbox
Motor Arm
Motor
60mm90Â╚5ÀÍ│Á┬Í-║¾┬Í┴¼¢Ë╠Õ(A░µ)
60mm90Â╚5ÀÍ│Á┬Í-╗íð╬┬Í╣╠Â¿░Õ(A░µ) x 2
60mm90Â╚5ÀÍ│Á┬Í-╗íð╬┬Í╝ð░Õ(A░µ) x 4
60mm90Â╚5ÀÍ│Á┬Í-╗íð╬┬Í(A░µ) x 10
60mm90Â╚5ÀÍ│Á┬Í-╗íð╬┬Í-¤·(A░µ) x 10
├¡Âñ3X5 x 10
─┌┴¨¢Ã┬¦╦┐(M3X20) x 3
WheelHub

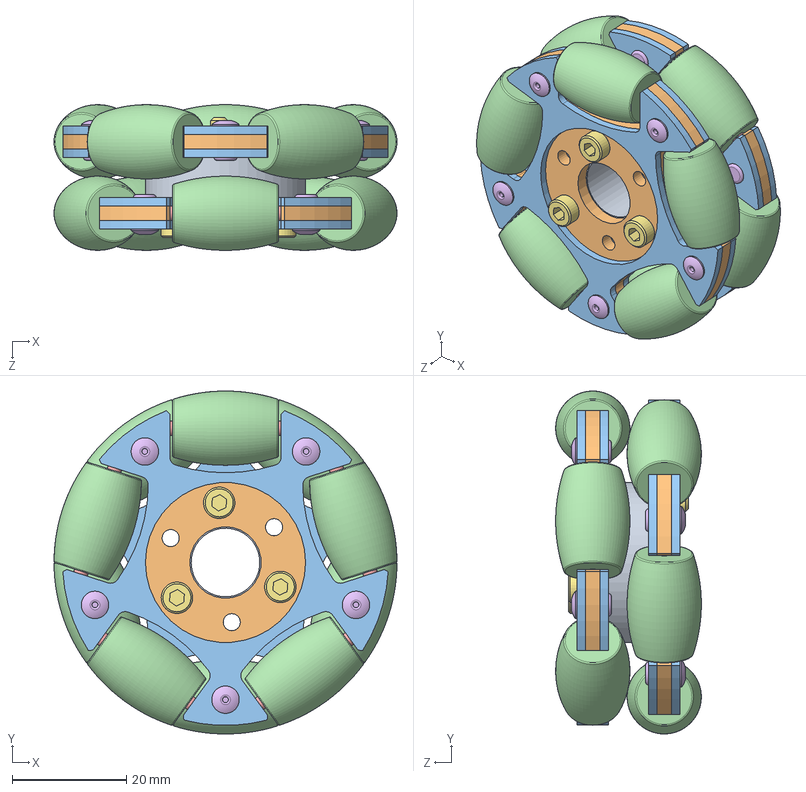
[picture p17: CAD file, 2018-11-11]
Development Files/Mini Triangle Solidworks - PCB Files/SolidWorks Model/60mm Aluminum Omni Wheel - SolidWorks Model.SLDASM
60.0 x 60.0 x 25.5 mm
60mm90Â╚5ÀÍ│Á┬Í-║¾┬Í┴¼¢Ë╠Õ(A░µ)
60mm90Â╚5ÀÍ│Á┬Í-╗íð╬┬Í╣╠Â¿░Õ(A░µ) x 2
60mm90Â╚5ÀÍ│Á┬Í-╗íð╬┬Í╝ð░Õ(A░µ) x 4
60mm90Â╚5ÀÍ│Á┬Í-╗íð╬┬Í(A░µ) x 10
60mm90Â╚5ÀÍ│Á┬Í-╗íð╬┬Í-¤·(A░µ) x 10
├¡Âñ3X5 x 10
─┌┴¨¢Ã┬¦╦┐(M3X20) x 3

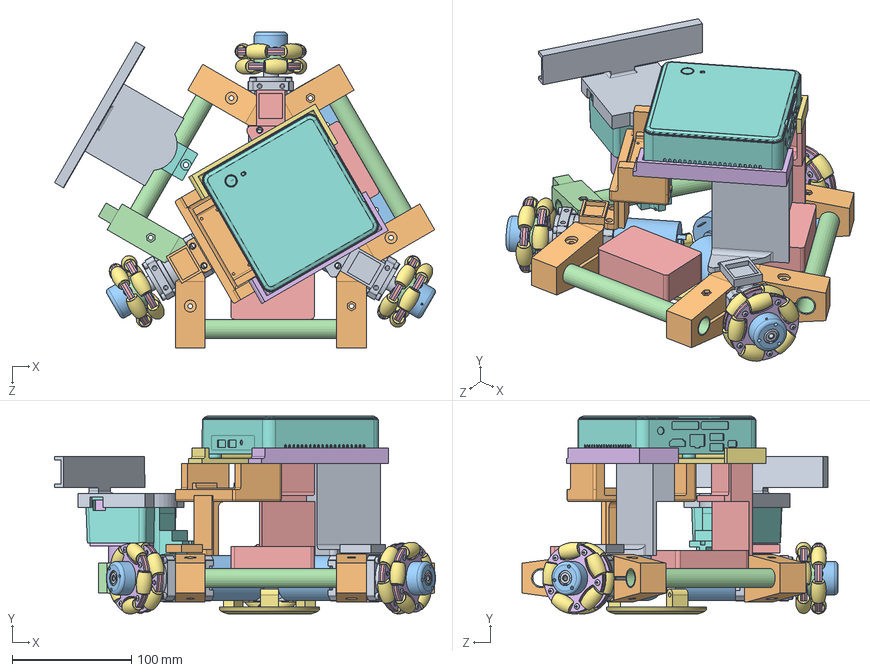
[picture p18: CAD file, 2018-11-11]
Development Files/Mini Triangle Solidworks - PCB Files/SolidWorks Model/Whole Assembly.SLDASM
319.0 x 165.7 x 264.4 mm
Gearbox x 3
Motor Arm x 5
Motor x 3
60mm90Â╚5ÀÍ│Á┬Í-║¾┬Í┴¼¢Ë╠Õ(A░µ) x 3
60mm90Â╚5ÀÍ│Á┬Í-╗íð╬┬Í╣╠Â¿░Õ(A░µ) x 6
60mm90Â╚5ÀÍ│Á┬Í-╗íð╬┬Í╝ð░Õ(A░µ) x 12
60mm90Â╚5ÀÍ│Á┬Í-╗íð╬┬Í(A░µ) x 30
60mm90Â╚5ÀÍ│Á┬Í-╗íð╬┬Í-¤·(A░µ) x 30
├¡Âñ3X5 x 30
─┌┴¨¢Ã┬¦╦┐(M3X20) x 9
WheelHub x 3
16mm tube 160mm x 3
Battery x 2
Lidar
lidar middle mount
Rear Rio Support Left
Front Rio Support
Motor Arm with sensor thingy
Rear Rio Support Right-extended
NUC6i5SYK-NUC6i3SYK-CHASSIS
realsense mount
boostConvHolder

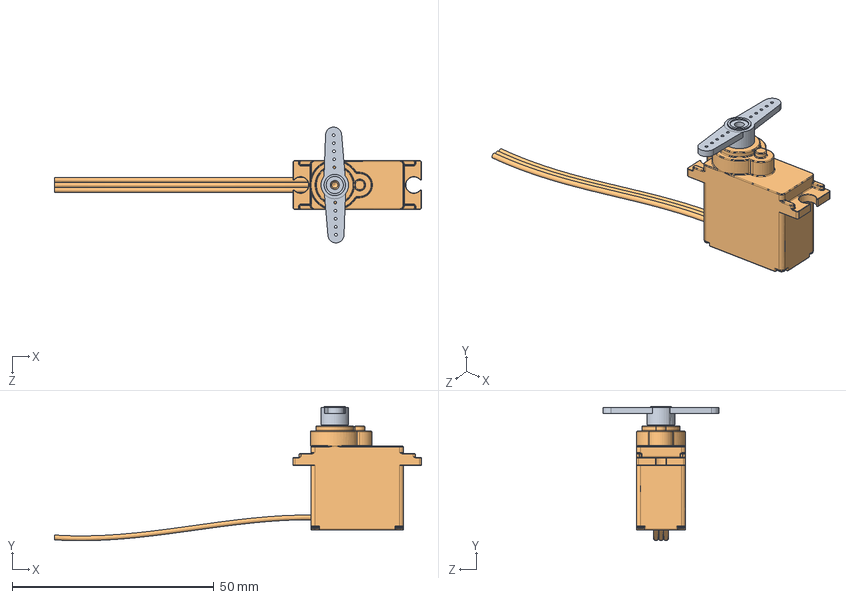
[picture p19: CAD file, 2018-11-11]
Development Files/Mini Triangle Solidworks - PCB Files/SolidWorks Model/Turnigy TGY-9025MG Servo.SLDASM
91.1 x 33.4 x 28.7 mm
TGY-9025MG Control Horn x 2
TGY-9025MG Servo Body

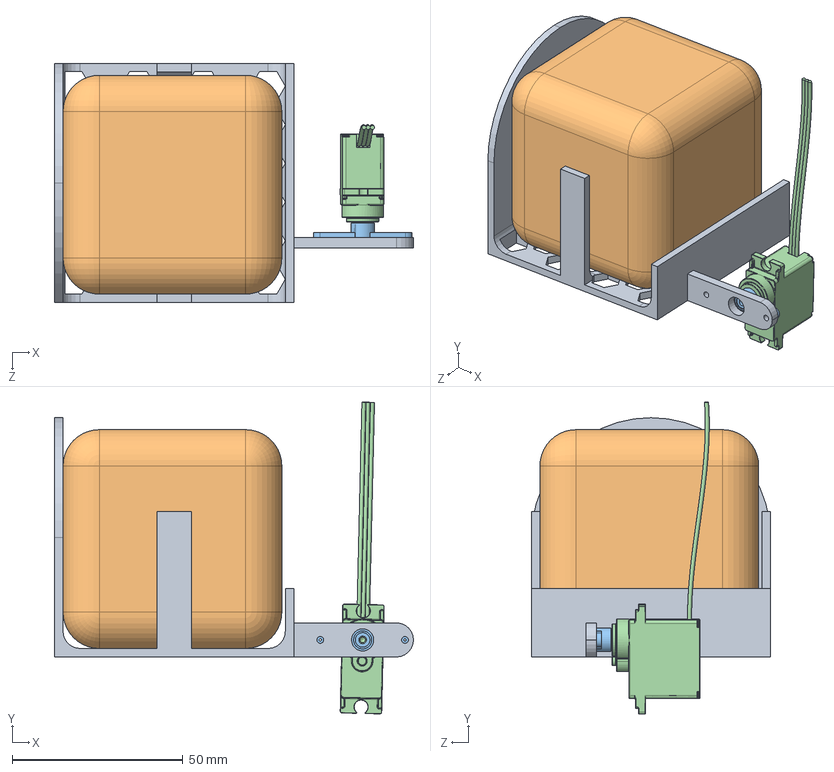
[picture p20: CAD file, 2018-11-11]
Development Files/Mini Triangle Solidworks - PCB Files/SolidWorks Model/Cube Holder Mechanism.SLDASM
105.0 x 91.2 x 70.0 mm
Cube Holder
TGY-9025MG Control Horn x 2
TGY-9025MG Servo Body

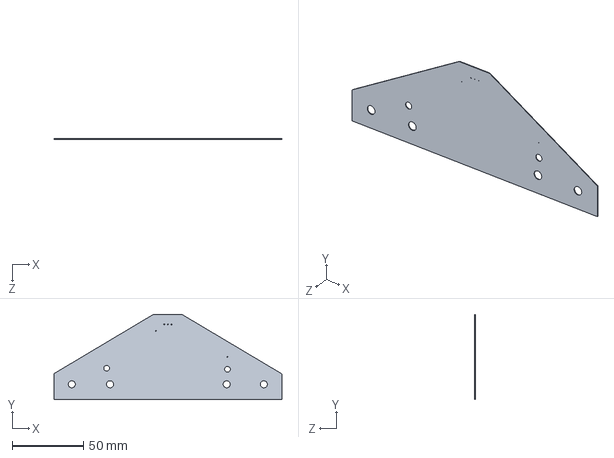
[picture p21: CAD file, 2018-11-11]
Development Files/Mini Triangle Solidworks - PCB Files/SolidWorks Model/Second One.SLDASM
160.3 x 60.1 x 0.411 mm

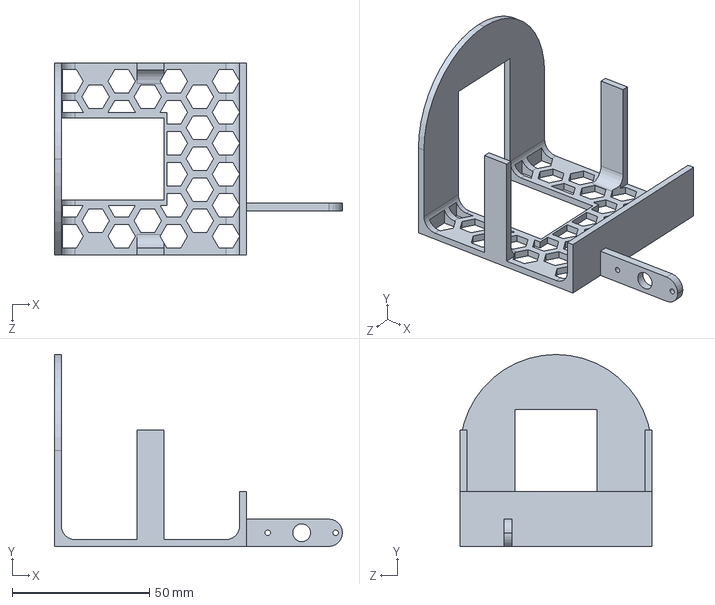
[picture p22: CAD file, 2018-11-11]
Development Files/Mini Triangle Solidworks - PCB Files/SolidWorks Model/Cube Holder.SLDPRT
105.0 x 70.0 x 70.0 mm

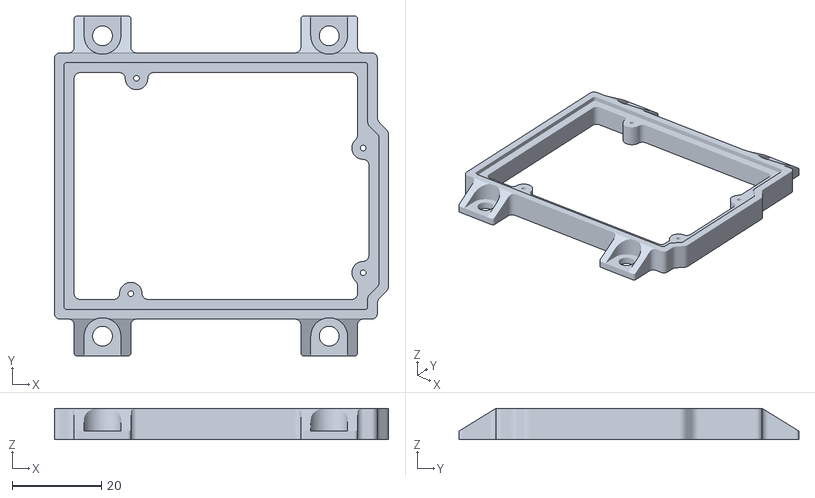
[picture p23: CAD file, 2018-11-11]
Development Files/Mini Triangle Solidworks - PCB Files/SolidWorks Model/SolidWorks Model/Arduino_Uno_Mount/UNO_R2_MOUNT.STL
74.9 x 76.2 x 6.99

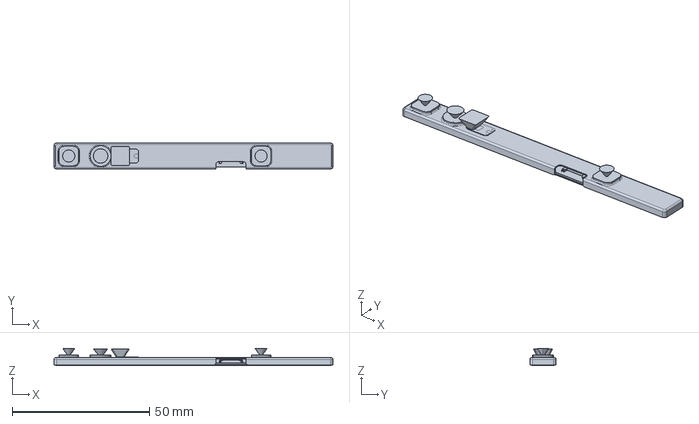
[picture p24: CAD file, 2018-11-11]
Development Files/Mini Triangle Solidworks - PCB Files/SolidWorks Model/SolidWorks Model/r200-3d-cad-files/r200_shrinkwrap_fov.stp
101.5 x 9.55 x 6.25 mm

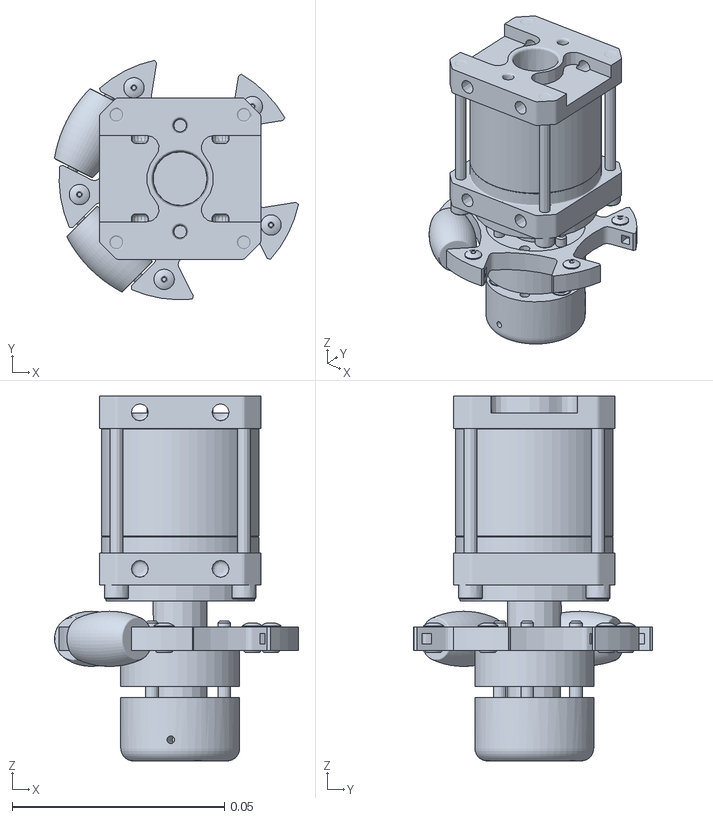
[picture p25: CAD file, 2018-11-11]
Development Files/Mini Triangle Solidworks - PCB Files/SolidWorks Model/Whole Assembly/meshes/back_wheel.STL
0.0574 x 0.0563 x 0.0859

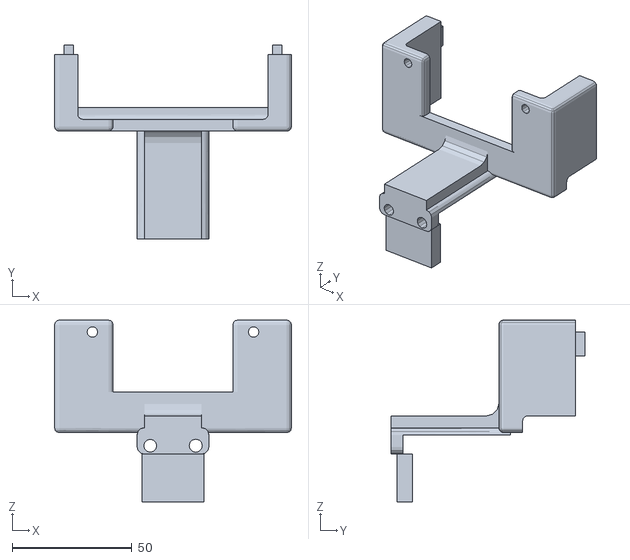
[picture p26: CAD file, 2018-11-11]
Laptop/catkin_ws/src/miniT/Front Rio Support.STL
99.0 x 81.0 x 76.0

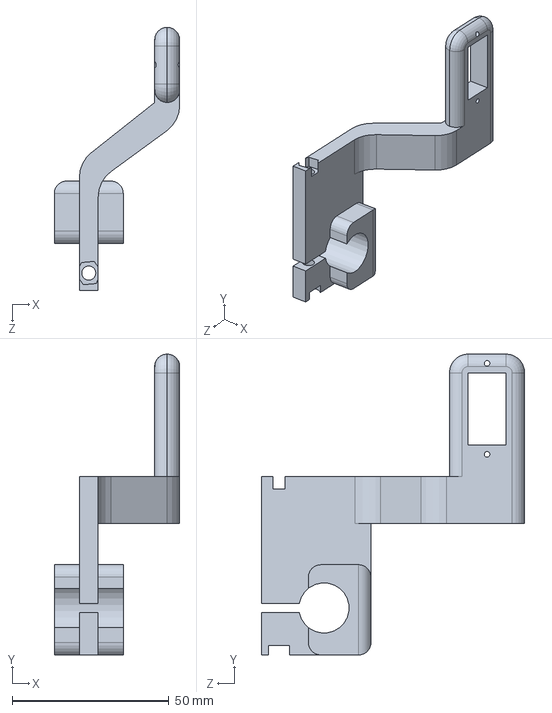
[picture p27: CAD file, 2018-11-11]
Development Files/Mini Triangle Solidworks - PCB Files/SolidWorks Model/Servo Mount 2.SLDPRT
40.0 x 96.0 x 84.0 mm

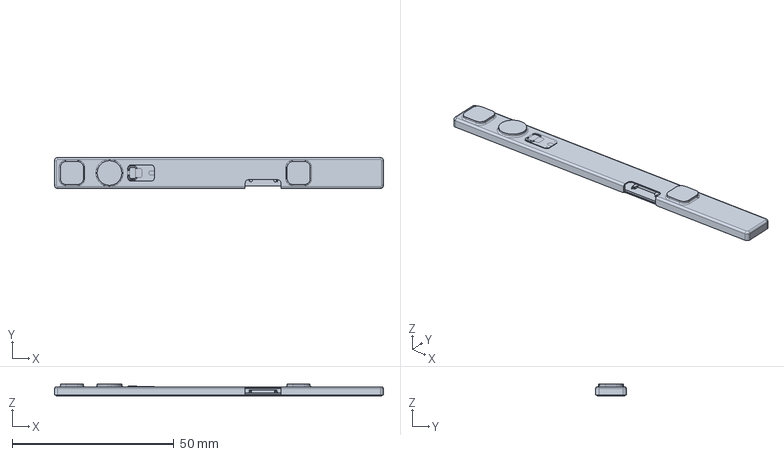
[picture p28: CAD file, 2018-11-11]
Development Files/Mini Triangle Solidworks - PCB Files/SolidWorks Model/SolidWorks Model/r200-3d-cad-files/r200_shrinkwrap.stp
101.5 x 9.55 x 3.80 mm

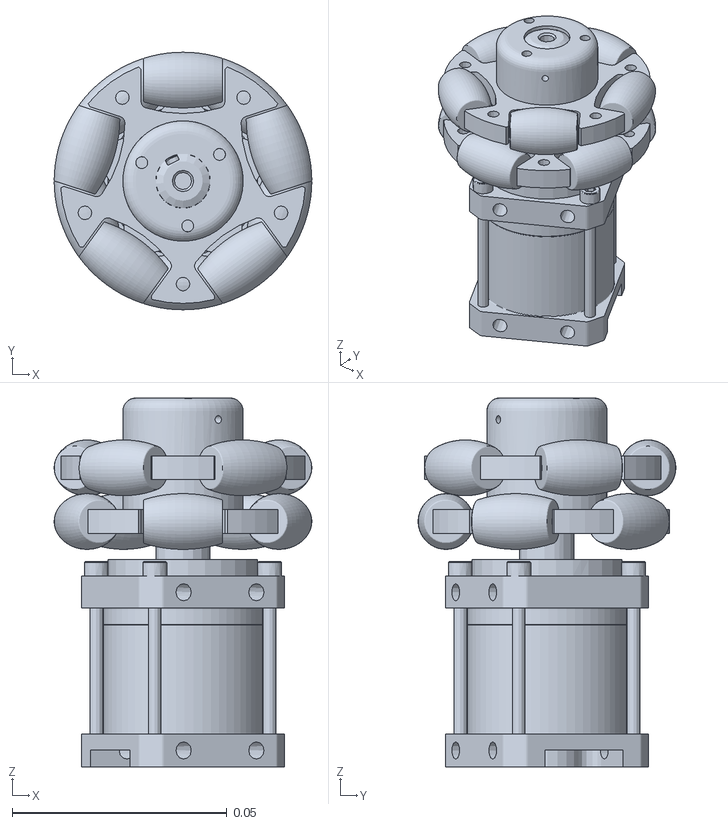
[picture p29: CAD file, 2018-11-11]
Development Files/Mini Triangle Solidworks - PCB Files/SolidWorks Model/Whole Assembly/meshes/right_wheel.STL
0.06 x 0.06 x 0.0859

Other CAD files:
Development Files/Mini Triangle Solidworks - PCB Files/SolidWorks Model/60mm90Â╚5ÀÍ│Á┬Í-ÁÑ╝■╗íð╬┬ÍÎÚ║¤(A░µ).sldasm
Development Files/Mini Triangle Solidworks - PCB Files/SolidWorks Model/60mm90Â╚5ÀÍ│Á┬Í-ÂÓ╝■╗íð╬┬ÍÎÚ║¤(A░µ ).sldasm
Laptop/catkin_ws/src/miniT/PART5.STL
Laptop/catkin_ws/src/simpleModel/meshes/rear_wheel.STL
Development Files/Mini Triangle Solidworks - PCB Files/SolidWorks Model/16mm tube 160mm.SLDPRT
Development Files/Mini Triangle Solidworks - PCB Files/SolidWorks Model/60mm90Â╚5ÀÍ│Á┬Í-║¾┬Í┴¼¢Ë╠Õ(A░µ).sldprt
Development Files/Mini Triangle Solidworks - PCB Files/SolidWorks Model/60mm90Â╚5ÀÍ│Á┬Í-╗íð╬┬Í(A░µ).sldprt
Development Files/Mini Triangle Solidworks - PCB Files/SolidWorks Model/60mm90Â╚5ÀÍ│Á┬Í-╗íð╬┬Í-¤·(A░µ).sldprt
Development Files/Mini Triangle Solidworks - PCB Files/SolidWorks Model/60mm90Â╚5ÀÍ│Á┬Í-╗íð╬┬Í╝ð░Õ(A░µ).sldprt
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

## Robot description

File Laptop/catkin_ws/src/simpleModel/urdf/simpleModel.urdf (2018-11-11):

<robot name="simpleModel">
  <link name="base_link">
    <inertial>
      <origin xyz="0.12576783984691 0.157079279388995 0.253293013901622" rpy="0 0 0" />
      <mass value="3.47488081535132" />
      <inertia ixx="0" ixy="0" ixz="0" iyy="0" iyz="0" izz="0" />
    </inertial>
    <visual>
      <origin xyz="0 0 0" rpy="0 0 0" />
      <geometry>
        <mesh filename="package://simpleModel/meshes/base_link.STL" />
      </geometry>
      <material name="">
        <color rgba="0.792156862745098 0.819607843137255 0.933333333333333 1" />
      </material>
    </visual>
    <collision>
      <origin xyz="0 0 0" rpy="0 0 0" />
      <geometry>
        <mesh filename="package://simpleModel/meshes/base_link.STL" />
      </geometry>
    </collision>
  </link>
  <link name="left_wheel">
    <inertial>
      <origin xyz="5.55111512312578E-17 -0.0590000000000001 -1.94289029309402E-16" rpy="0 0 0" />
      <mass value="0.164669720530563" />
      <inertia ixx="0" ixy="0" ixz="0" iyy="0" iyz="0" izz="0" />
    </inertial>
    <visual>
      <origin xyz="0 0 0" rpy="0 0 0" />
      <geometry>
        <mesh filename="package://simpleModel/meshes/left_wheel.STL" />
      </geometry>
      <material name="">
        <color rgba="0.1 0.819607843137255 0.933333333333333 1" />
      </material>
    </visual>
    <collision>
      <origin xyz="0 0 0" rpy="0 0 0" />
      <geometry>
        <mesh filename="package://simpleModel/meshes/left_wheel.STL" />
      </geometry>
    </collision>
  </link>
  <joint name="left" type="continuous">
    <origin xyz="-0.0455337877398974 -0.16958975480187 0.157079279388995" rpy="-2.81885393441649E-15 4.32963728535954E-17 0.785398163397448" />
    <parent link="base_link" />
    <child link="left_wheel" />
    <axis xyz="0 -1 0" />
  </joint>
  <link name="right_wheel">
    <inertial>
      <origin xyz="0 -0.0311417692656913 -5.55111512312578E-17" rpy="0 0 0" />
      <mass value="0.164669720530563" />
      <inertia ixx="0" ixy="0" ixz="0" iyy="0" iyz="0" izz="0" />
    </inertial>
    <visual>
      <origin xyz="0 0 0" rpy="1.57079632679 0 0" />
      <geometry>
        <mesh filename="package://simpleModel/meshes/right_wheel.STL" />
      </geometry>
      <material name="">
        <color rgba="0.792156862745098 0.1 0.933333333333333 1" />
      </material>
    </visual>
    <collision>
      <origin xyz="0 0 0" rpy="0 0 0" />
      <geometry>
        <mesh filename="package://simpleModel/meshes/right_wheel.STL" />
      </geometry>
    </collision>
  </link>
  <joint name="right" type="continuous">
    <origin xyz="0.233329611117793 -0.233329611117793 0.157079279388995" rpy="0.785398163397448 -1.5707963267949 0" />
    <parent link="base_link" />
    <child link="right_wheel" />
    <axis xyz="0 0 1" />
  </joint>
  <link name="rear_wheel">
    <inertial>
      <origin xyz="-2.77555756156289E-17 0.0130000000000003 2.77555756156289E-17" rpy="0 0 0" />
      <mass value="0.164669720530563" />
      <inertia ixx="0" ixy="0" ixz="0" iyy="0" iyz="0" izz="0" />
    </inertial>
    <visual>
      <origin xyz="0 -0.025 0" rpy="0 0 0" />
      <geometry>
        <mesh filename="package://simpleModel/meshes/rear_wheel.STL" />
      </geometry>
      <material name="">
        <color rgba="0.792156862745098 0.819607843137255 0.1 1" />
      </material>
    </visual>
    <collision>
      <origin xyz="0 0 0" rpy="0 0 0" />
      <geometry>
        <mesh filename="package://simpleModel/meshes/rear_wheel.STL" />
      </geometry>
    </collision>
  </link>
  <joint name="rear" type="continuous">
    <origin xyz="0.125767839846911 -0.395318025852579 0.157079279388994" rpy="0 -1.5707963267949 0" />
    <parent link="base_link" />
    <child link="rear_wheel" />
    <axis xyz="0 1 0" />
  </joint>
</robot>

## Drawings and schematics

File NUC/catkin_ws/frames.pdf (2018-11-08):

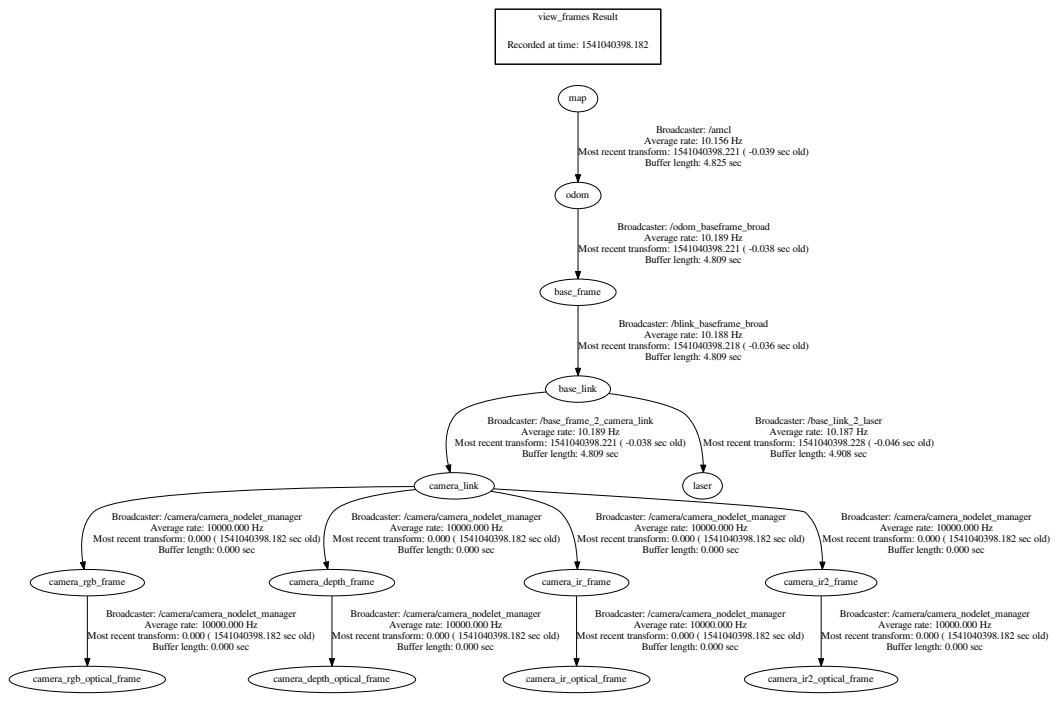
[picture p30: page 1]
view_frames Result; camera_link; camera_rgb_frame; camera_depth_frame; camera_ir_frame; camera_ir2_frame; camera_rgb_optical_frame; base_link; laser; camera_depth_optical_frame; camera_ir_optical_frame; camera_ir2_optical_frame; base_frame; odom; map

Recorded at time: 1541040398.182

Broadcaster: /amcl
Average rate: 10.156 Hz
Buffer length: 4.825 sec

Most recent transform: 1541040398.221 ( -0.039 sec old)

Broadcaster: /odom_baseframe_broad
Average rate: 10.189 Hz
Buffer length: 4.809 sec

Most recent transform: 1541040398.221 ( -0.038 sec old)

Broadcaster: /blink_baseframe_broad
Average rate: 10.188 Hz

Most recent transform: 1541040398.218 ( -0.036 sec old)

Broadcaster: /base_frame_2_camera_link

Broadcaster: /base_link_2_laser
Average rate: 10.187 Hz
Buffer length: 4.908 sec

Most recent transform: 1541040398.228 ( -0.046 sec old)

Broadcaster: /camera/camera_nodelet_manager
Most recent transform: 0.000 ( 1541040398.182 sec old)

Average rate: 10000.000 Hz
Buffer length: 0.000 sec

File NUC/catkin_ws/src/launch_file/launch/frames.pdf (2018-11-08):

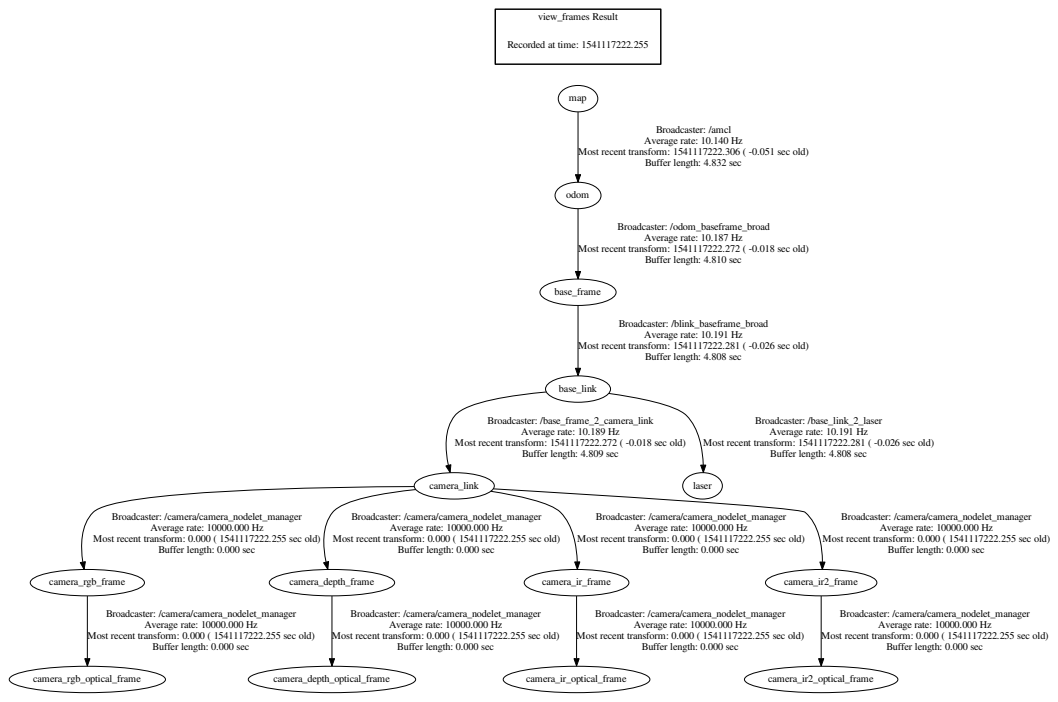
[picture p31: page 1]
view_frames Result; camera_link; camera_rgb_frame; camera_depth_frame; camera_ir_frame; camera_ir2_frame; camera_rgb_optical_frame; base_link; laser; camera_depth_optical_frame; camera_ir_optical_frame; camera_ir2_optical_frame; odom; base_frame; map

Recorded at time: 1541117222.255

Broadcaster: /amcl
Average rate: 10.140 Hz
Buffer length: 4.832 sec

Most recent transform: 1541117222.306 ( -0.051 sec old)

Broadcaster: /odom_baseframe_broad
Average rate: 10.187 Hz
Buffer length: 4.810 sec

Most recent transform: 1541117222.272 ( -0.018 sec old)

Broadcaster: /blink_baseframe_broad
Average rate: 10.191 Hz
Buffer length: 4.808 sec

Most recent transform: 1541117222.281 ( -0.026 sec old)

Broadcaster: /base_frame_2_camera_link
Average rate: 10.189 Hz
Buffer length: 4.809 sec

Broadcaster: /base_link_2_laser

Broadcaster: /camera/camera_nodelet_manager
Most recent transform: 0.000 ( 1541117222.255 sec old)

Average rate: 10000.000 Hz
Buffer length: 0.000 sec

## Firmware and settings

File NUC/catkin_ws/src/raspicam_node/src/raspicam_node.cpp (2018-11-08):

/*
Copyright (c) 2013, Broadcom Europe Ltd
Copyright (c) 2013, James Hughes
All rights reserved.

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
THIS SOFTWARE IS PROVIDED BY THE COPYRIGHT HOLDERS AND CONTRIBUTORS "AS IS" AND
ANY EXPRESS OR IMPLIED WARRANTIES, INCLUDING, BUT NOT LIMITED TO, THE IMPLIED
WARRANTIES OF MERCHANTABILITY AND FITNESS FOR A PARTICULAR PURPOSE ARE
DISCLAIMED. IN NO EVENT SHALL THE COPYRIGHT HOLDER OR CONTRIBUTORS BE LIABLE FOR
ANY DIRECT, INDIRECT, INCIDENTAL, SPECIAL, EXEMPLARY, OR CONSEQUENTIAL DAMAGES
(INCLUDING, BUT NOT LIMITED TO, PROCUREMENT OF SUBSTITUTE GOODS OR SERVICES;
LOSS OF USE, DATA, OR PROFITS; OR BUSINESS INTERRUPTION) HOWEVER CAUSED AND
ON ANY THEORY OF LIABILITY, WHETHER IN CONTRACT, STRICT LIABILITY, OR TORT
(INCLUDING NEGLIGENCE OR OTHERWISE) ARISING IN ANY WAY OUT OF THE USE OF THIS
SOFTWARE, EVEN IF ADVISED OF THE POSSIBILITY OF SUCH DAMAGE.
*/

/**
 * \file RaspiVid.c
 * Command line program to capture a camera video stream and encode it to file.
 * Also optionally display a preview/viewfinder of current camera input.
 *
 * \date 28th Feb 2013
 * \Author: James Hughes
 *
 * Description
 *
 * 3 components are created; camera, preview and video encoder.
 * Camera component has three ports, preview, video and stills.
 * This program connects preview and stills to the preview and video
 * encoder. Using mmal we don't need to worry about buffers between these
 * components, but we do need to handle buffers from the encoder, which
 * are simply written straight to the file in the requisite buffer callback.
 *
 * We use the RaspiCamControl code to handle the specific camera settings.
 * We use the RaspiPreview code to handle the (generic) preview window
 */

#ifdef __x86_64__

#include <stdio.h>

int main(int argc, char **argv) {
    (void)fprintf(stderr,
                  "The raspicam_node for the x86/64 architecture is a fake!\n");
    return 1;
}

#endif  // __x86_64__

#ifdef __arm__

// We use some GNU extensions (basename)
#include <memory.h>
#include <stdio.h>
#include <stdlib.h>
#include <string.h>
#define VCOS_ALWAYS_WANT_LOGGING

#define VERSION_STRING "v1.2"

#include "bcm_host.h"
#include "interface/vcos/vcos.h"

#include "interface/mmal/mmal.h"
#include "interface/mmal/mmal_buffer.h"
#include "interface/mmal/mmal_logging.h"
#include "interface/mmal/util/mmal_connection.h"
#include "interface/mmal/util/mmal_default_components.h"
#include "interface/mmal/util/mmal_util.h"
#include "interface/mmal/util/mmal_util_params.h"

#include "camera_info_manager/camera_info_manager.h"
#include "ros/ros.h"
#include "sensor_msgs/CameraInfo.h"
#include "sensor_msgs/CompressedImage.h"
#include "sensor_msgs/SetCameraInfo.h"
#include "std_srvs/Empty.h"

#include "RaspiCLI.h"
#include "RaspiCamControl.h"

#include <dynamic_reconfigure/server.h>
#include <raspicam_node/CameraConfig.h>

#include <semaphore.h>

const int IMG_BUFFER_SIZE = 10 * 1024 * 1024;
/// Camera number to use - we only have one camera, indexed from 0.
#define CAMERA_NUMBER 0

// Standard port setting for the camera component
#define MMAL_CAMERA_PREVIEW_PORT 0
#define MMAL_CAMERA_VIDEO_PORT 1
#define MMAL_CAMERA_CAPTURE_PORT 2

// Video format information
#define VIDEO_FRAME_RATE_NUM 30
#define VIDEO_FRAME_RATE_DEN 1

/// Video render needs at least 2 buffers.
#define VIDEO_OUTPUT_BUFFERS_NUM 3

int mmal_status_to_int(MMAL_STATUS_T status);

/** Structure containing all state information for the current run
 */
typedef struct {
    int isInit;
    int width;      /// Requested width of image
    int height;     /// requested height of image
    int framerate;  /// Requested frame rate (fps)
    int quality;

    RASPICAM_CAMERA_PARAMETERS camera_parameters;  /// Camera setup parameters

    MMAL_COMPONENT_T *camera_component;     /// Pointer to the camera component
    MMAL_COMPONENT_T *encoder_component;    /// Pointer to the encoder component
    MMAL_CONNECTION_T *preview_connection;  /// Pointer to the connection from
                                            /// camera to preview
    MMAL_CONNECTION_T *encoder_connection;  /// Pointer to the connection from
                                            /// camera to encoder

    MMAL_POOL_T *video_pool;  /// Pointer to the pool of buffers used by encoder
                              /// output port
    MMAL_POOL_T *encoder_pool;  /// Pointer to the pool of buffers used by
                                /// encoder output port
    ros::Publisher *image_pub;
} RASPIVID_STATE;

RASPIVID_STATE state_srv;
ros::Publisher image_pub;
ros::Publisher camera_info_pub;
sensor_msgs::CameraInfo c_info;
std::string tf_prefix;
std::string camera_frame_id;
int skip_frames = 0;
int frames_skipped = 0;

/** Struct used to pass information in encoder port userdata to callback
 */
typedef struct {
    unsigned char *buffer[2];  /// File handle to write buffer data to.
    RASPIVID_STATE
        *pstate;  /// pointer to our state in case required in callback
    int abort;  /// Set to 1 in callback if an error occurs to attempt to abort
                /// the capture
    int frame;
    int id;
} PORT_USERDATA;

static void display_valid_parameters(char *app_name);

/**
 * Assign a default set of parameters to the state passed in
 *
 * @param state Pointer to state structure to assign defaults to
 */
static void get_status(RASPIVID_STATE *state) {
    int temp;
    std::string str;
    bool temp_bool;
    if (!state) {
        vcos_assert(0);
        return;
    }

    // Default everything to zero
    memset(state, 0, sizeof(RASPIVID_STATE));

    if (ros::param::get("~width", temp)) {
        state->width = temp;
    } else {
        state->width = 640;
        ros::param::set("~width", 640);
    }

    if (ros::param::get("~height", temp)) {
        state->height = temp;
    } else {
        state->height = 480;
        ros::param::set("~height", 480);
    }

    if (ros::param::get("~quality", temp)) {
        if (temp > 0 && temp <= 100)
            state->quality = temp;
        else
            state->quality = 80;
    } else {
        state->quality = 80;
        ros::param::set("~quality", 80);
    }

    if (ros::param::get("~framerate", temp)) {
        if (temp > 0 && temp <= 90)
            state->framerate = temp;
        else
            state->framerate = 30;
    } else {
        state->framerate = 30;
        ros::param::set("~framerate", 30);
    }

    if (ros::param::get("~tf_prefix", str)) {
        tf_prefix = str;
    } else {
        tf_prefix = "";
        ros::param::set("~tf_prefix", "");
    }

    if (ros::param::get("~camera_frame_id", str)) {
        camera_frame_id = str;
    } else {
        camera_frame_id = "";
        ros::param::set("~camera_frame_id", "");
    }

    state->isInit = 0;

    // Setup preview window defaults
    // raspipreview_set_defaults(&state->preview_parameters);

    // Set up the camera_parameters to default
    raspicamcontrol_set_defaults(&state->camera_parameters);

    if (ros::param::get("~hFlip", temp_bool)) {
        state->camera_parameters.hflip = temp_bool;
    } else {
        state->camera_parameters.hflip = 0;
        ros::param::set("~hFlip", 0);
    }

    if (ros::param::get("~vFlip", temp_bool)) {
        state->camera_parameters.vflip = temp_bool;
    } else {
        state->camera_parameters.vflip = 0;
        ros::param::set("~vFlip", 0);
    }

    if (ros::param::get("~shutter_speed", temp)) {
        state->camera_parameters.shutter_speed = temp;
    } else {
        state->camera_parameters.shutter_speed = 0;
        ros::param::set("~shutter_speed", 0);
    }
}

/**
 *  buffer header callback function for encoder
 *
 *  Callback will dump buffer data to the specific file
 *
 * @param port Pointer to port from which callback originated
 * @param buffer mmal buffer header pointer
 */
static void encoder_buffer_callback(MMAL_PORT_T *port,
                                    MMAL_BUFFER_HEADER_T *buffer) {
    MMAL_BUFFER_HEADER_T *new_buffer;
    int complete = 0;

    // We pass our file handle and other stuff in via the userdata field.

    PORT_USERDATA *pData = (PORT_USERDATA *)port->userdata;
    if (pData && pData->pstate->isInit) {
        int bytes_written = buffer->length;
        if (buffer->length) {
            if (pData->id != INT_MAX) {
                if (pData->id + buffer->length > IMG_BUFFER_SIZE) {
                    ROS_ERROR(
                        "pData->id (%d) + buffer->length (%d) > "
                        "IMG_BUFFER_SIZE (%d), skipping the frame",
                        pData->id, buffer->length, IMG_BUFFER_SIZE);
                    pData->id = INT_MAX;  // mark this frame corrupted
                } else {
                    mmal_buffer_header_mem_lock(buffer);
                    memcpy(&(pData->buffer[pData->frame & 1][pData->id]),
                           buffer->data, buffer->length);
                    pData->id += bytes_written;
                    mmal_buffer_header_mem_unlock(buffer);
                }
            }
        }

        if (bytes_written != buffer->length) {
            vcos_log_error("Failed to write buffer data (%d from %d)- aborting",
                           bytes_written, buffer->length);
            ROS_ERROR("Failed to write buffer data (%d from %d)- aborting",
                      bytes_written, buffer->length);
            pData->abort = 1;
        }
        if (buffer->flags & (MMAL_BUFFER_HEADER_FLAG_FRAME_END |
                             MMAL_BUFFER_HEADER_FLAG_TRANSMISSION_FAILED))
            complete = 1;

        if (complete) {
            if (pData->id != INT_MAX) {
                // ROS_INFO("Frame size %d", pData->id);
                if (skip_frames > 0 && frames_skipped < skip_frames) {
                    frames_skipped++;
                } else {
                    frames_skipped = 0;
                    sensor_msgs::CompressedImage msg;
                    msg.header.seq = pData->frame;
                    msg.header.frame_id = camera_frame_id;
                    msg.header.stamp = ros::Time::now();
                    msg.format = "jpg";
                    msg.data.insert(
                        msg.data.end(), pData->buffer[pData->frame & 1],
                        &(pData->buffer[pData->frame & 1][pData->id]));
                    image_pub.publish(msg);
                    c_info.header.seq = pData->frame;
                    c_info.header.stamp = msg.header.stamp;
                    c_info.header.frame_id = msg.header.frame_id;
                    camera_info_pub.publish(c_info);
                    pData->frame++;
                }
            }
            pData->id = 0;
        }
    }

    // release buffer back to the pool
    mmal_buffer_header_release(buffer);

    // and send one back to the port (if still open)
    if (port->is_enabled) {
        MMAL_STATUS_T status;

        new_buffer = mmal_queue_get(pData->pstate->encoder_pool->queue);

        if (new_buffer) status = mmal_port_send_buffer(port, new_buffer);

        if (!new_buffer || status != MMAL_SUCCESS) {
            vcos_log_error("Unable to return a buffer to the encoder port");
            ROS_ERROR("Unable to return a buffer to the encoder port");
        }
    }
}

/**
 * Create the camera component, set up its ports
 *
 * @param state Pointer to state control struct
 *
 * @return 0 if failed, pointer to component if successful
 *
 */
static MMAL_COMPONENT_T *create_camera_component(RASPIVID_STATE *state) {
    MMAL_COMPONENT_T *camera = 0;
    MMAL_ES_FORMAT_T *format;
    MMAL_PORT_T *preview_port = NULL, *video_port = NULL, *still_port = NULL;
    MMAL_STATUS_T status;

    /* Create the component */
    status = mmal_component_create(MMAL_COMPONENT_DEFAULT_CAMERA, &camera);

    if (status != MMAL_SUCCESS) {
        vcos_log_error("Failed to create camera component");
        ROS_ERROR("Failed to create camera component");
        goto error;
    }

    if (!camera->output_num) {
        vcos_log_error("Camera doesn't have output ports");
        ROS_ERROR("Camera doesn't have output ports");
        goto error;
    }

    video_port = camera->output[MMAL_CAMERA_VIDEO_PORT];
    still_port = camera->output[MMAL_CAMERA_CAPTURE_PORT];

    //  set up the camera configuration
    {
        MMAL_PARAMETER_CAMERA_CONFIG_T cam_config;
        cam_config.hdr.id = MMAL_PARAMETER_CAMERA_CONFIG;
        cam_config.hdr.size = sizeof(cam_config);
        cam_config.max_stills_w = state->width;
        cam_config.max_stills_h = state->height;
        cam_config.stills_yuv422 = 0;
        cam_config.one_shot_stills = 0;
        cam_config.max_preview_video_w = state->width;
        cam_config.max_preview_video_h = state->height;
        cam_config.num_preview_video_frames = 3;
        cam_config.stills_capture_circular_buffer_height = 0;
        cam_config.fast_preview_resume = 0;
        cam_config.use_stc_timestamp = MMAL_PARAM_TIMESTAMP_MODE_RESET_STC;

        mmal_port_parameter_set(camera->control, &cam_config.hdr);
    }

    // Now set up the port formats

    // Set the encode format on the video  port

    format = video_port->format;
    format->encoding_variant = MMAL_ENCODING_I420;

    format->encoding = MMAL_ENCODING_I420;
    format->es->video.width = state->width;
    format->es->video.height = state->height;
    format->es->video.crop.x = 0;
    format->es->video.crop.y = 0;
    format->es->video.crop.width = state->width;
    format->es->video.crop.height = state->height;
    format->es->video.frame_rate.num = state->framerate;
    format->es->video.frame_rate.den = VIDEO_FRAME_RATE_DEN;

    status = mmal_port_format_commit(video_port);

    if (status) {
        vcos_log_error("camera video format couldn't be set");
        ROS_ERROR("camera video format couldn't be set");
        goto error;
    }

    // Ensure there are enough buffers to avoid dropping frames
    if (video_port->buffer_num < VIDEO_OUTPUT_BUFFERS_NUM)
        video_port->buffer_num = VIDEO_OUTPUT_BUFFERS_NUM;

    // Set the encode format on the still  port

    format = still_port->format;

    format->encoding = MMAL_ENCODING_OPAQUE;
    format->encoding_variant = MMAL_ENCODING_I420;

    format->es->video.width = state->width;
    format->es->video.height = state->height;
    format->es->video.crop.x = 0;
    format->es->video.crop.y = 0;
    format->es->video.crop.width = state->width;
    format->es->video.crop.height = state->height;
    format->es->video.frame_rate.num = 1;
    format->es->video.frame_rate.den = 1;

    status = mmal_port_format_commit(still_port);

    if (status) {
        vcos_log_error("camera still format couldn't be set");
        ROS_ERROR("camera still format couldn't be set");
        goto error;
    }

    video_port->buffer_num = video_port->buffer_num_recommended;
    /* Ensure there are enough buffers to avoid dropping frames */
    if (still_port->buffer_num < VIDEO_OUTPUT_BUFFERS_NUM)
        still_port->buffer_num = VIDEO_OUTPUT_BUFFERS_NUM;

    /* Enable component */
    status = mmal_component_enable(camera);

    if (status) {
        vcos_log_error("camera component couldn't be enabled");
        ROS_ERROR("camera component couldn't be enabled");
        goto error;
    }

    raspicamcontrol_set_all_parameters(camera, &state->camera_parameters);

    state->camera_component = camera;

    ROS_INFO("Camera component done\n");

    return camera;

error:

    if (camera) mmal_component_destroy(camera);

    return 0;
}

/**
 * Destroy the camera component
 *
 * @param state Pointer to state control struct
 *
 */
static void destroy_camera_component(RASPIVID_STATE *state) {
    if (state->camera_component) {
        mmal_component_destroy(state->camera_component);
        state->camera_component = NULL;
    }
}

/**
 * Create the encoder component, set up its ports
 *
 * @param state Pointer to state control struct
 *
 * @return MMAL_SUCCESS if all OK, something else otherwise
 *
 */
static MMAL_STATUS_T create_encoder_component(RASPIVID_STATE *state) {
    MMAL_COMPONENT_T *encoder = 0;
    MMAL_PORT_T *encoder_input = NULL, *encoder_output = NULL;
    MMAL_STATUS_T status;
    MMAL_POOL_T *pool;

    status =
        mmal_component_create(MMAL_COMPONENT_DEFAULT_IMAGE_ENCODER, &encoder);

    if (status != MMAL_SUCCESS) {
        vcos_log_error("Unable to create video encoder component");
        ROS_ERROR("Unable to create video encoder component");
        goto error;
    }

    if (!encoder->input_num || !encoder->output_num) {
        status = MMAL_ENOSYS;
        vcos_log_error("Video encoder doesn't have input/output ports");
        ROS_ERROR("Video encoder doesn't have input/output ports");
        goto error;
    }

    encoder_input = encoder->input[0];
    encoder_output = encoder->output[0];

    // We want same format on input and output
    mmal_format_copy(encoder_output->format, encoder_input->format);

    // Only supporting H264 at the moment
    encoder_output->format->encoding = MMAL_ENCODING_JPEG;

    encoder_output->buffer_size = encoder_output->buffer_size_recommended;

    if (encoder_output->buffer_size < encoder_output->buffer_size_min)
        encoder_output->buffer_size = encoder_output->buffer_size_min;

    encoder_output->buffer_num = encoder_output->buffer_num_recommended;

    if (encoder_output->buffer_num < encoder_output->buffer_num_min)
        encoder_output->buffer_num = encoder_output->buffer_num_min;

    // Commit the port changes to the output port
    status = mmal_port_format_commit(encoder_output);

    if (status != MMAL_SUCCESS) {
        vcos_log_error("Unable to set format on video encoder output port");
        ROS_ERROR("Unable to set format on video encoder output port");
        goto error;
    }

    // Set the JPEG quality level
    status = mmal_port_parameter_set_uint32(
        encoder_output, MMAL_PARAMETER_JPEG_Q_FACTOR, state->quality);

    if (status != MMAL_SUCCESS) {
        vcos_log_error("Unable to set JPEG quality");
        ROS_ERROR("Unable to set JPEG quality");
        goto error;
    }

    //  Enable component
    status = mmal_component_enable(encoder);

    if (status != MMAL_SUCCESS) {
        vcos_log_error("Unable to enable video encoder component");
        ROS_ERROR("Unable to enable video encoder component");
        goto error;
    }

    /* Create pool of buffer headers for the output port to consume */
    pool = mmal_port_pool_create(encoder_output, encoder_output->buffer_num,
                                 encoder_output->buffer_size);

    if (!pool) {
        vcos_log_error(
            "Failed to create buffer header pool for encoder output port %s",
            encoder_output->name);
        ROS_ERROR(
            "Failed to create buffer header pool for encoder output port %s",
            encoder_output->name);
    }

    state->encoder_pool = pool;
    state->encoder_component = encoder;

    ROS_INFO("Encoder component done\n");

    return status;

error:
    if (encoder) mmal_component_destroy(encoder);

    return status;
}

/**
 * Destroy the encoder component
 *
 * @param state Pointer to state control struct
 *
 */
static void destroy_encoder_component(RASPIVID_STATE *state) {
    // Get rid of any port buffers first
    if (state->video_pool) {
        mmal_port_pool_destroy(state->encoder_component->output[0],
                               state->video_pool);
    }

    if (state->encoder_component) {
        mmal_component_destroy(state->encoder_component);
        state->encoder_component = NULL;
    }
}
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
int main(int argc, char **argv) {
    ros::init(argc, argv, "raspicam_node");
    ros::NodeHandle n("~");

    n.param("skip_frames", skip_frames, 0);

    std::string camera_info_url;
    std::string camera_name;

    n.param("camera_info_url", camera_info_url,
            std::string("package://raspicam_node/camera_info/camera.yaml"));
    n.param("camera_name", camera_name, std::string("camera"));
    ROS_INFO("Loading CameraInfo from %s", camera_info_url.c_str());

    camera_info_manager::CameraInfoManager c_info_man(n, camera_name,
                                                      camera_info_url);

    // get_status(&state_srv);
    init_cam(&state_srv);  // will need to figure out how to handle start and
                           // stop with dynamic reconfigure

    if (!c_info_man.loadCameraInfo(camera_info_url)) {
        ROS_INFO("Calibration file missing. Camera not calibrated");
    } else {
        c_info = c_info_man.getCameraInfo();
        ROS_INFO("Camera successfully calibrated from default file");
    }

    if (!c_info_man.loadCameraInfo("")) {
        ROS_INFO("No device specifc calibration found");
    } else {
        c_info = c_info_man.getCameraInfo();
        ROS_INFO("Camera successfully calibrated from device specifc file");
    }

    image_pub =
        n.advertise<sensor_msgs::CompressedImage>("image/compressed", 1);
    camera_info_pub = n.advertise<sensor_msgs::CameraInfo>("camera_info", 1);

    dynamic_reconfigure::Server<raspicam_node::CameraConfig> server;
    dynamic_reconfigure::Server<raspicam_node::CameraConfig>::CallbackType f;
    f = boost::bind(&reconfigure_callback, _1, _2);
    server.setCallback(f);

    start_capture(&state_srv);
    ros::spin();
    close_cam(&state_srv);
    return 0;
}

#endif  // __arm__
